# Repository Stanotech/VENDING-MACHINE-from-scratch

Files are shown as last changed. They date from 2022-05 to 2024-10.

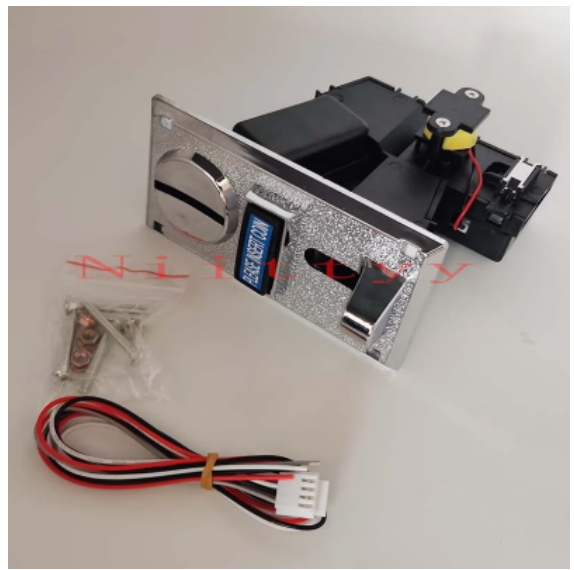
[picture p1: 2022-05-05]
photos/coin acceptor.jpg

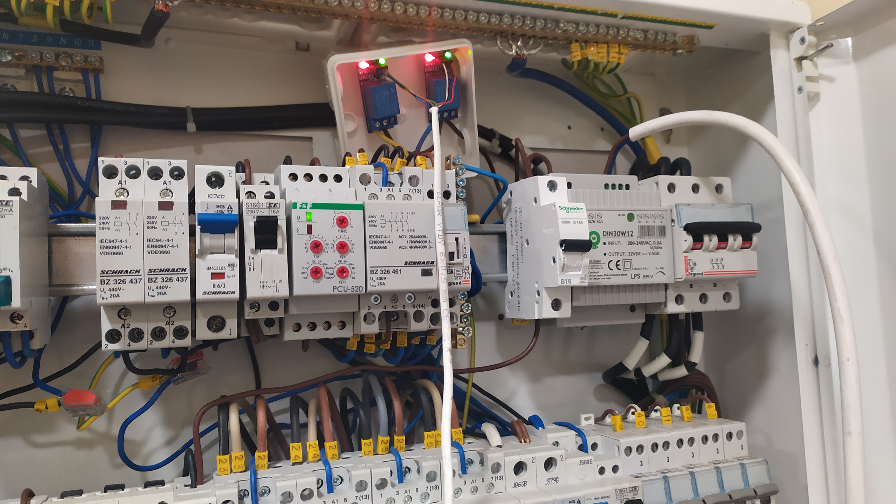
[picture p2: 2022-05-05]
photos/IMG_20211215_151331.jpg

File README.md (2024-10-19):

# VENDING-MACHINE-from-scratch
Vending machine for switching on lights on football and basketball court after payment.
This machine is entirely designed and created by me.



This vending machine is projected for switching lights on two courts. Those courts have different pricing. 
Vending machine is very simple in use. 
1. Select the court on which you want to switch on lights
2. Display show rectangle which indicates selected court
3. Put the money in. Coin and bill are accepted
4. Machine will automatically calculate time proportionally to money puted in
5. Lights turns on
6. Display shows remaining time

This vending machine is connected to existing electrical switchboard with manual switches. Vending machine relays are connected in parallel with the relays of the manual switches in the electrical switchboard.
Bill acceptor accept 10, 20, 50, 100 nominals giving 1, 2, 5, 10 sharp high impulses 100ms lenght.
Coin acceptor accept 1, 2, 5 nominals giving 1, 2, 5 sharp high impulses 100ms lenght.
Signals are filtered, counted and recalculated to time.

Vending machine has been working flawlessly for a year giving allot of evening entertainment :)
Location- Poland, Poznań, Golęcińska 9

What you need to build this vending machine ?
- Arduino UNO
- simple display like TM1637
- two relays like jqc-3ff-s-z
- coin acceptor (you will find it on aliexpress. Check the photo folder to see how it looks)
- NV9 bill acceptor
- waterproof casing- this one is US military case for something. I have bought it on some dumb. 
- additionaly just in case I made rain-proof front of coin acceptor. I have attached g-code for 3d printing it. 
- two waterproof buttons
- some wires :)

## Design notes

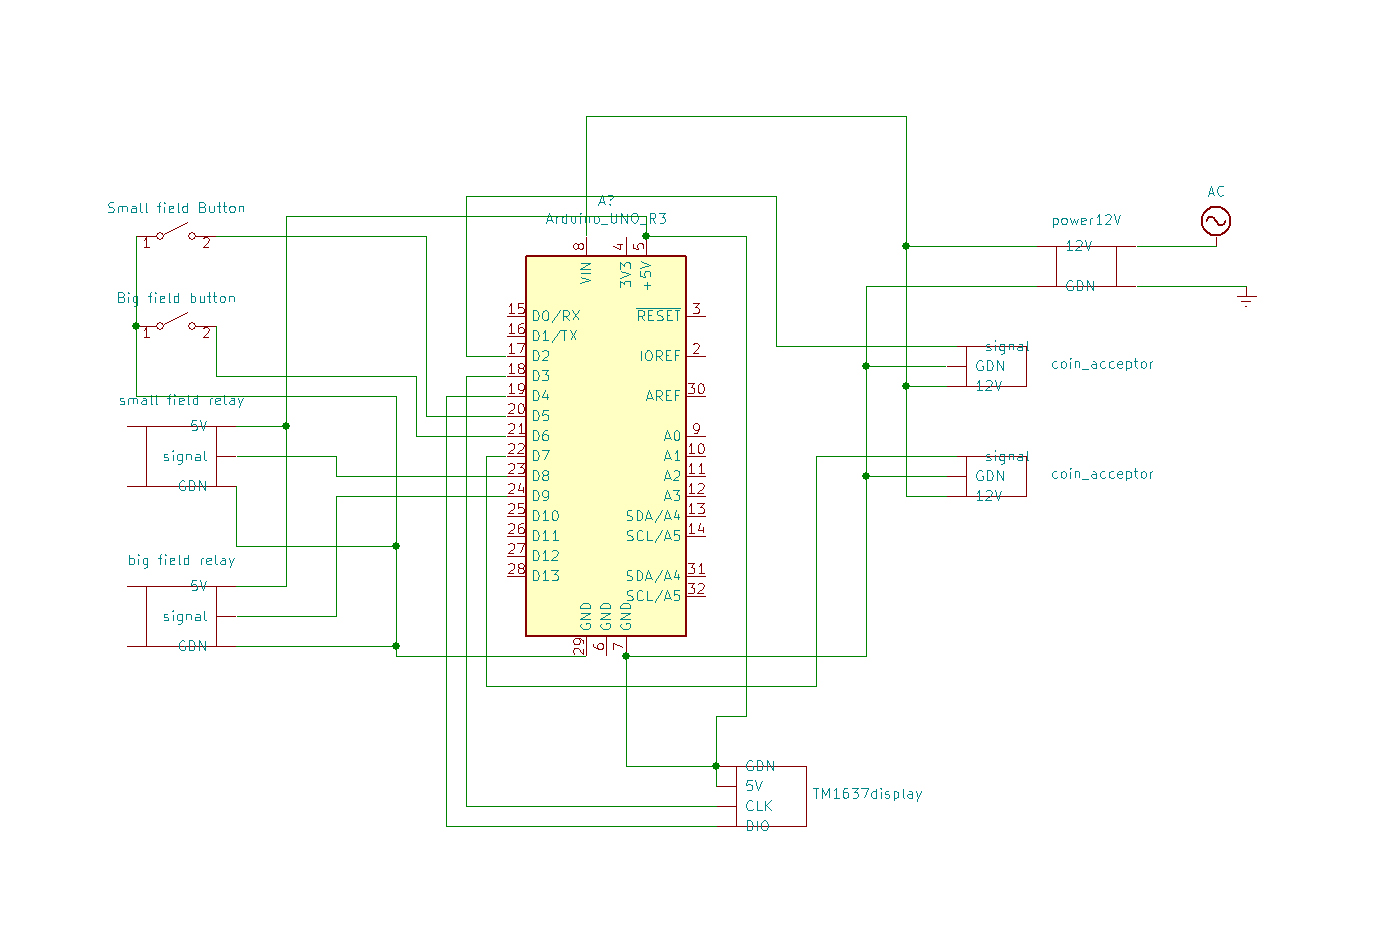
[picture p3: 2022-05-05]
electronic scheme.jpg

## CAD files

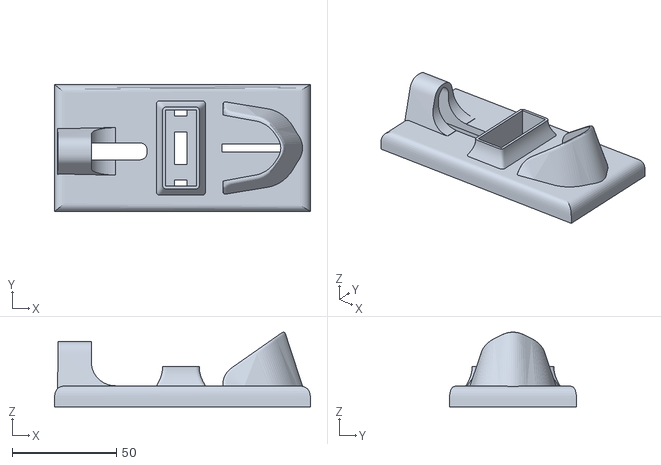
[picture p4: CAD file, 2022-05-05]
coin acceptor front project for 3d printing/1.STL
123.0 x 61.0 x 35.9

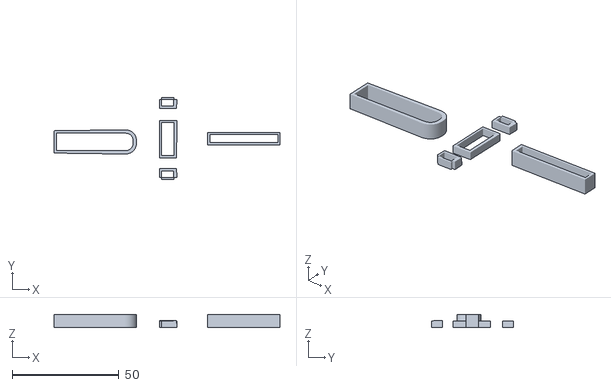
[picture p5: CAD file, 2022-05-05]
coin acceptor front project for 3d printing/2.STL
106.0 x 38.3 x 6.10

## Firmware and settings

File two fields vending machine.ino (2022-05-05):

#include <Arduino.h>
#include <TM1637Display.h>
#include <EEPROM.h>

#define CLK 3
#define DIO 4

TM1637Display display(CLK, DIO);

int DisplayTime1=0, DisplayTime2=0, minutes1=0, minutes2=0;
byte LastState=0, LastButton1=1, LastButton2=1, LastMinutes1 =0, LastMinutes2 =0, filtering=0, field=1;
unsigned long TimeMark = 0, TimeMark2 =0 , TimeMark3=0 ;
uint8_t rectangle[]={
  SEG_A|SEG_F|SEG_E|SEG_D,
  SEG_A|SEG_B|SEG_C|SEG_D,
};

void setup() {
  pinMode (8, OUTPUT);                  //small field relay
  pinMode (9, OUTPUT);                  //big field relay
  pinMode (5, INPUT_PULLUP);            //button small field
  pinMode (6, INPUT_PULLUP);            //button big field
  pinMode (2, INPUT_PULLUP);            //coin signal
  Serial.begin(500000);                 // comunitation speed
  display.setBrightness(0x0f);
  display.clear();
  byte LastState = digitalRead (2);
  }
void FieldCheck (){
  
  }
void ImpulseCheck () {
  byte state = digitalRead(2);
  if ((state != LastState) && (state == 0) && (filtering == 0)) {
    filtering = 1;
    TimeMark=millis();                                            //Start timer for impulse lenght
  }
  if (filtering == 1 && (95 <= (millis()-TimeMark) <= 105)) {     //filter all signal with lenght <98, 102> ms
    if ((state != LastState) && (state == 1)) {                   // if state has changed to 1 do
      if (field ==1){
        minutes1+= 4;
      }
      if (field ==2){
        minutes2+= 4;
      }      
      filtering=0;
      }
    }
  LastState = state;
  }



// /////////////////////////////////

  
void loop() {
  ImpulseCheck ();

  if (minutes1>0){                                      //          TIME COUNTER FOR FIELD1
    if (TimeMark2 ==0) {
      TimeMark2 = millis();                                         //start timer counting one minute
      digitalWrite(8, LOW);
      }
    if ((millis()-TimeMark2) >= 60000){                             //check if one minute elapsed
      minutes1--;
      TimeMark2 = millis();                                         // if minute elapsed then zero Timer2 to count next minute
      }
    }
  if (minutes1 == 0) {
    digitalWrite(8, HIGH);                                           //turn off the light
    TimeMark2 = 0;                                                  //zero timer2 (minute counter)        
  }

  if (minutes2>0){                                       //          TIME COUNTER FOR FIELD2
    if (TimeMark3 ==0) {
      TimeMark3 = millis();                                         //start timer counting one minute
      digitalWrite(9, LOW);
      }
    if ((millis()-TimeMark3) >= 60000){                             //check if one minute elapsed
      minutes2--;
      TimeMark3 = millis();                                         // if minute elapsed then zero Timer2 to count next minute
      }
    }
  if (minutes2 == 0) {
    digitalWrite(9, HIGH);                                           //turn off the light
    TimeMark3 = 0;                                                  //zero timer2 (minute counter)  
  }



  if (((digitalRead(6)) != (LastButton1)) && (digitalRead(6) == 0)){              //left button check
    field = 1;    
    display.clear();
    display.setSegments(rectangle, 2, 0); 
  }
  if (((digitalRead(5)) != (LastButton2)) && (digitalRead(5) == 0)){              //right button check
    field = 2;
    display.clear();
    display.setSegments(rectangle, 2, 2); 
  }
  LastButton1 = digitalRead(6);
  LastButton2 = digitalRead(5);


  
                                                                    // WHAT TO DISPLAY
  
  DisplayTime1= ((minutes1/60)*100)+(minutes1%60);                 //count 4 digit time format hh:mm
  DisplayTime2= ((minutes2/60)*100)+(minutes2%60);                 //count 4 digit time format hh:mm                                                                   
  
  if (field ==1){                                                  // if the button of field 1 is pressed than it display field 1 time
    if (minutes1 > 0){
      display.showNumberDecEx(DisplayTime1, 0b01000000, true, 4, 0);       
    }
    if  (((minutes1) != (LastMinutes1)) && (minutes1 == 0)){
      display.clear();
      display.setSegments(rectangle, 2, 0);                         //display left rectangle
    }
  }
  if (field == 2){
    if (minutes2 > 0){
      display.showNumberDecEx(DisplayTime2, 0b01000000, true, 4, 0);       
    }
    if  (((minutes2) != (LastMinutes2)) && (minutes2 == 0)){
      display.clear();
      display.setSegments(rectangle, 2, 2);                         //display right rectangle
    }
  }
  LastMinutes1 = minutes1;
  LastMinutes2 = minutes2;
}
